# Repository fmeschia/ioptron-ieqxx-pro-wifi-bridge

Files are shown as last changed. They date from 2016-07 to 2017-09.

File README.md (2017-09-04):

# Wi-Fi to RS-232 bridge for iOptron iEQ Pro mounts

An ESP8266 and [esp-link](https://github.com/jeelabs/esp-link)-based Wi-Fi to RS-232 bridge to allow TCP wireless control of an iOptron iEQ Pro mount (tested on iEQ45 Pro, should also work on iEQ30 Pro).

[Here](https://www.youtube.com/watch?v=_uhQ0Lzc3-E) you can find a video of the operation an iEQ45 Pro mount with this circuit and the commercial Sky Safari app.

## Features
* Uses an inexpensive ESP8266 ESP-01 module
* Uses the well tested [esp-link](https://github.com/jeelabs/esp-link) open source firmware to implement a transparent TCP-to-serial bridge
* Powered directly from the mount, via the iOptron port, with an efficient 3.3V DC-to-DC converter based on the MC34063 switch-mode converter
* RS-232 compatibility ensured by a MAX3232 driver/receiver
* Easy to build, with through-hole parts and protoboard-friendly design

## Disclaimer
This project comes with no warranty. The project files may contain mistakes and errors. If you build this circuit, it is solely your responsibility to make sure that it doesn't damage your mount or other equipment, and doesn't hurt you or other people. Test all voltages and polarities before making any connections. By building the circuit you accept that I will have no liability whatsoever for damages or injuries that you or other parties may incur in during the building process or during the operation of the circuit. Builder assumes all risks. Don't build this circuit if you don't agree!

## Building instructions
### 1. Flash the ESP-01 module
The ESP-01 module must be flashed with the esp-link firmware. I have tested version 2.2.3 and it works well.
In order to flash the module, I recommend following the instructions present on the [release page](https://github.com/jeelabs/esp-link/releases/tag/v2.2.3) of the esp-link GitHub repository. Remember to enable flash programming mode by tying GPIO0 to ground and rebooting the module, before trying to upload the firmware code. The following is a schematic of how one should connect the ESP-01 module to a FTDI232 3.3V breakout board like the one sold by Sparkfun:

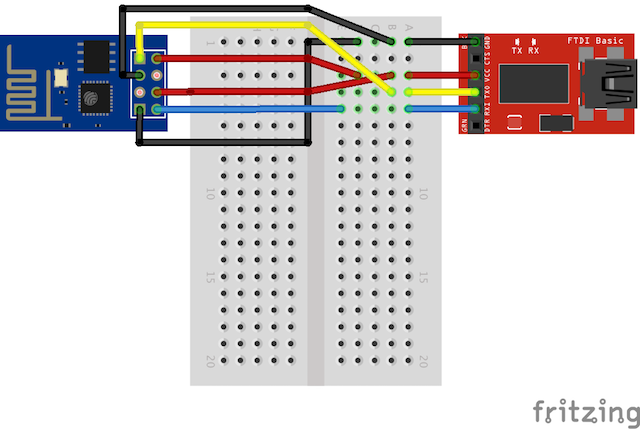
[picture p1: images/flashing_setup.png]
Flashing setup Hardware setup for flashing via USB


In my case, I used a 8-Mbit ESP-01 module, and in order to flash it (from a macOS system) I first installed esptool 1.1:

    $ curl -L https://github.com/themadinventor/esptool/archive/v1.1.tar.gz | tar xzf -
    $ cd esptool-1.1
    $ sudo python setup.py install

And then I used the following commands:

    $ curl -L https://github.com/jeelabs/esp-link/releases/download/v2.2.3/esp-link-v2.2.3.tgz | tar xzf -
    $ cd esp-link-v2.2.3
    $ esptool.py --port /dev/tty.usbserial-A601LLNU --baud 460800 write_flash -fs 8m -ff 40m 0x00000 boot_v1.5.bin 0x1000 user1.bin 0x7E000 blank.bin
    esptool.py v1.1
    Connecting...
    Running Cesanta flasher stub...
    Flash params set to 0x0020
    Writing 4096 @ 0x0... 4096 (100 %)
    Wrote 4096 bytes at 0x0 in 0.1 seconds (292.3 kbit/s)...
    Writing 307200 @ 0x1000... 307200 (100 %)
    Wrote 307200 bytes at 0x1000 in 7.1 seconds (347.0 kbit/s)...
    Writing 4096 @ 0x7e000... 4096 (100 %)
    Wrote 4096 bytes at 0x7e000 in 0.1 seconds (298.3 kbit/s)...
    Leaving...

### 2. Configure the esp-link bridge
After successfully flashing the ESP8266 module, you should power it down, remove the connection from GPI0 to ground, then power it up again and configure it. I recommend *not* powering it from USB via the FTDI232 board for this, because it doesn't really supply enough current for the ESP8266 in normal operation. Instead, power it from a regulated 3.3V (*not* 5V, it would burn it instantly!) power supply capable of delivering 0.5A.
Once powered up, a new Wi-Fi network with name "ESP_xxxx" should be visible. After connecting to that network, point your browser to http://192.168.4.1. If everything works fine, the browser should show the esp-link web interface. As a bare minimum, there are three configuration steps to do:

1. Configure the pin preset to "esp-01" 

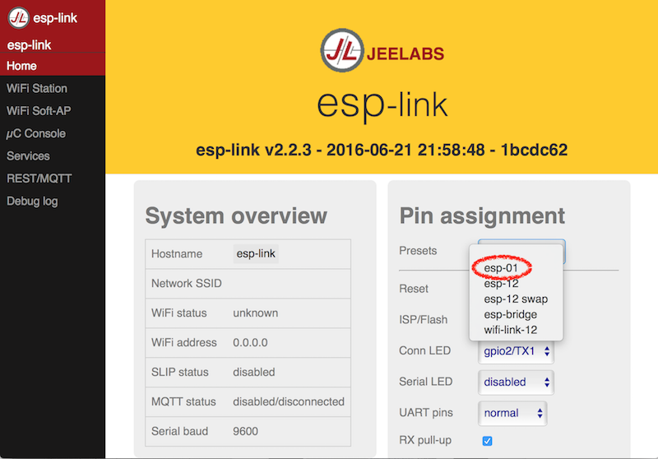
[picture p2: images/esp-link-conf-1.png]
Esp-link-pin-preset esp-link pin preset
    

2. Configure the serial port to 9600 bps, 8 data bits, 1 stop bit, no parity (9600 8N1) 

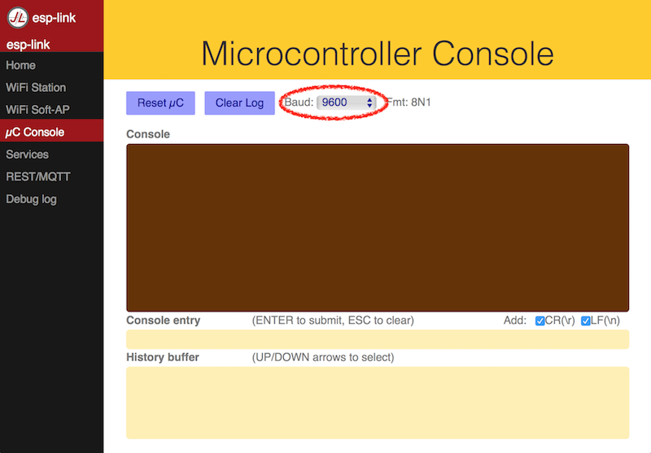
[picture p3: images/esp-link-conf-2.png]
Esp-link-bps esp-link serial port rate
    

3. Disable the UART debug log 

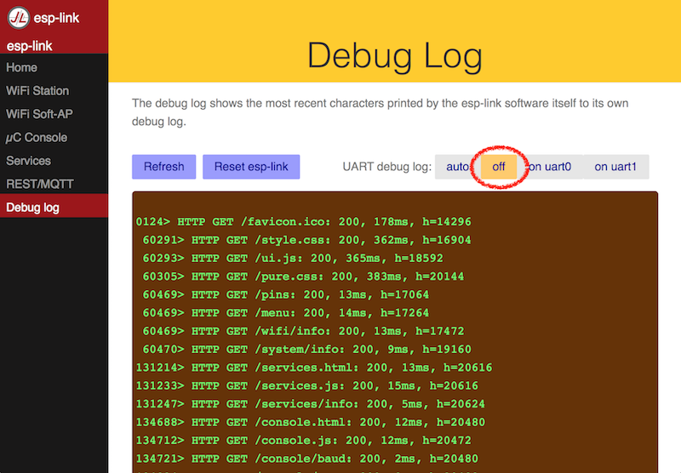
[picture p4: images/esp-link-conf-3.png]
Esp-link-debug-log esp-link debug log preset
    

You will also probably want to change the WiFi network name and its security, but that's up to personal preference.

### 3. Build the circuit
The EAGLE board file is easy to follow and transfer to a protoboard. The "traces" on the bottom layer are meant to be solder bridges between adjacent copper pads of the protoboard, whereas the air wires are meant to be real jumper wires. When the wire connects directly to a part lead, it is meant to be routed on the bottom of the board. When there are vias, the idea is that the wire can be routed on the top of the board, but of course that's just a suggestion.

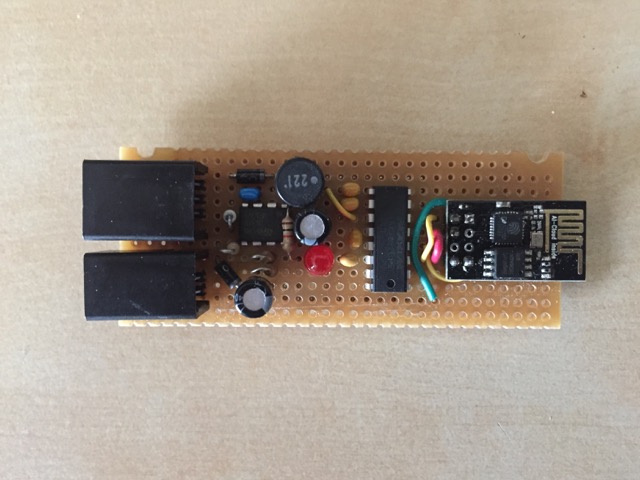
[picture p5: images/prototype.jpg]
Prototype Prototype on protoboard

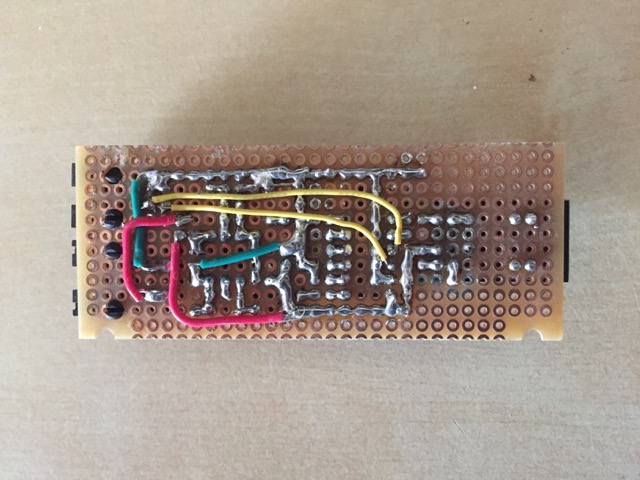
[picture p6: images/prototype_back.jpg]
Prototype back Backside of the prototype board


The project also includes an Eagle file for a simple through-hole-parts PCB. It is essentially a single-sided board: all the traces are routed on the solder side, and the component side has just a ground plane. The ground plane, on both sides, stops short of the ESP8266 trace antenna.

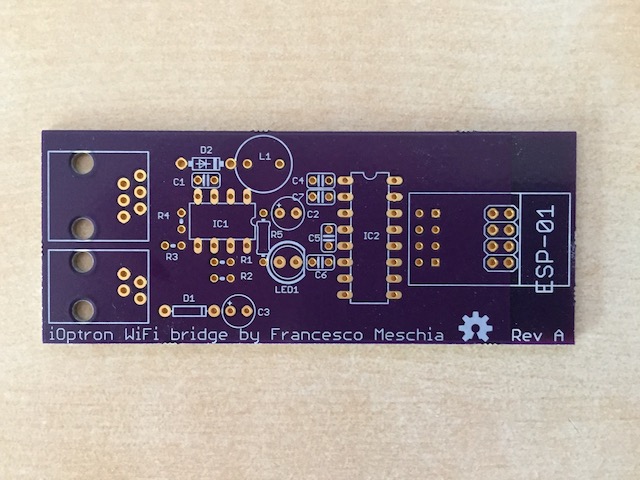
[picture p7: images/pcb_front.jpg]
PCB front Front side of the PCB

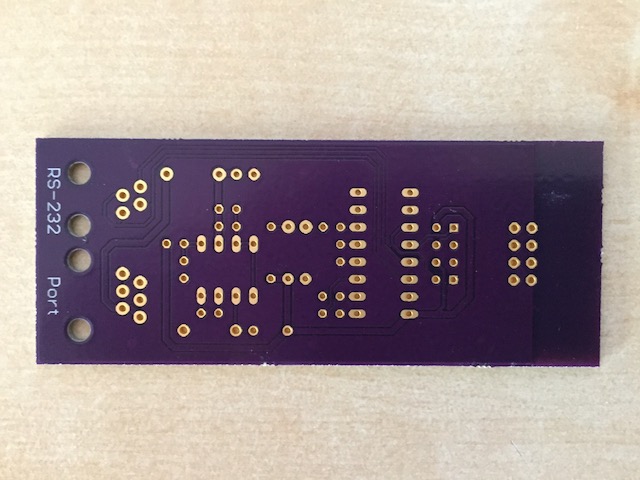
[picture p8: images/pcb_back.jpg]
PCB back Back side of the PCB

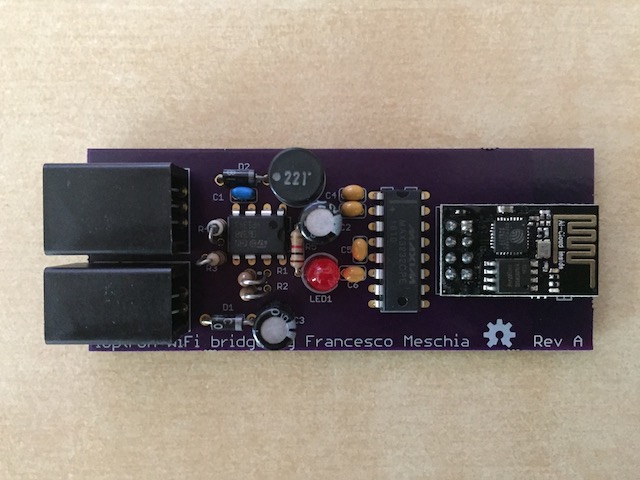
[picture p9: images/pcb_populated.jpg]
PCB populated The populated PCB


## Usage
### Connection
To connect the circuit to the mount, you need to use two cords: 
* a "straight" 6P6C cord to connect the circuit to the iOptron port on the mount (for 12V power)
* a "straight" 4P4C cord to connect the circuit to the RS-232 port on the mount

"Straight" cords are cords in which the order of the colors of the inner wires is the same if you look at both plugs (when observed from the same side). The coiled cords that came with the mount came are straight cords:

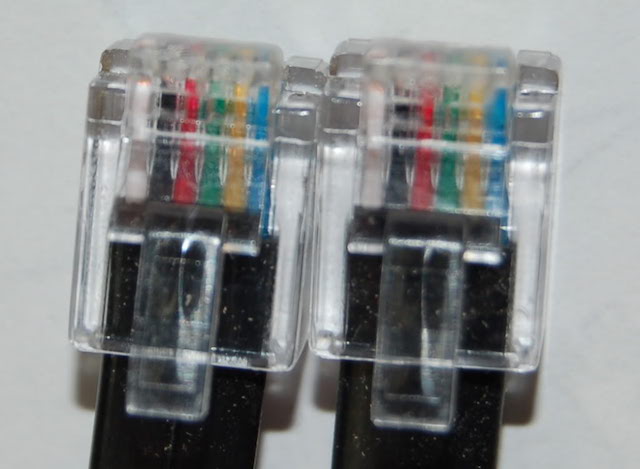
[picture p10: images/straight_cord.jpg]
Straight cord plugs Plugs of a straight cord


*A 6P6C straight cord*
### Power it up
The bridge draws power directly from the mount. When the mount is powered up, the board is also energized and the LED should light up.
### Test it
If you have a digital mixed-signal oscilloscope, you can test if the board works properly by capturing the output of the RXD pin of the RS-232 port while connected to the ESP8266 Wi-Fi AP and while sending a string to the TCP port 23 of the ESP8266 IP address (by default, 192.168.4.1). Here is a sample screenshot of the output of a USB logic analyzer while sending the string "HELLO" (ASCII 0x48 0x45 0x4C 0x4C 0x4F plus a 0x0A newline) to the bridge board:

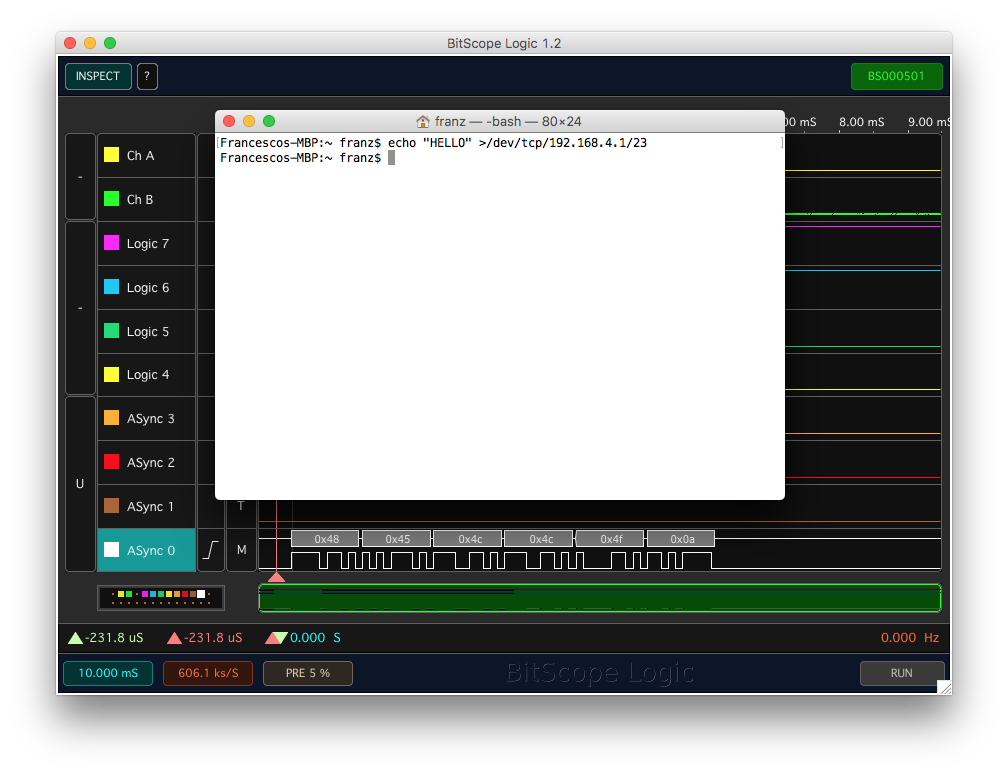
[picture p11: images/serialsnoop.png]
Logic analyzer output

### Enjoy!
Point your favorite telescope control software to 192.168.4.1, port 23, and enjoy wireless telescope control!

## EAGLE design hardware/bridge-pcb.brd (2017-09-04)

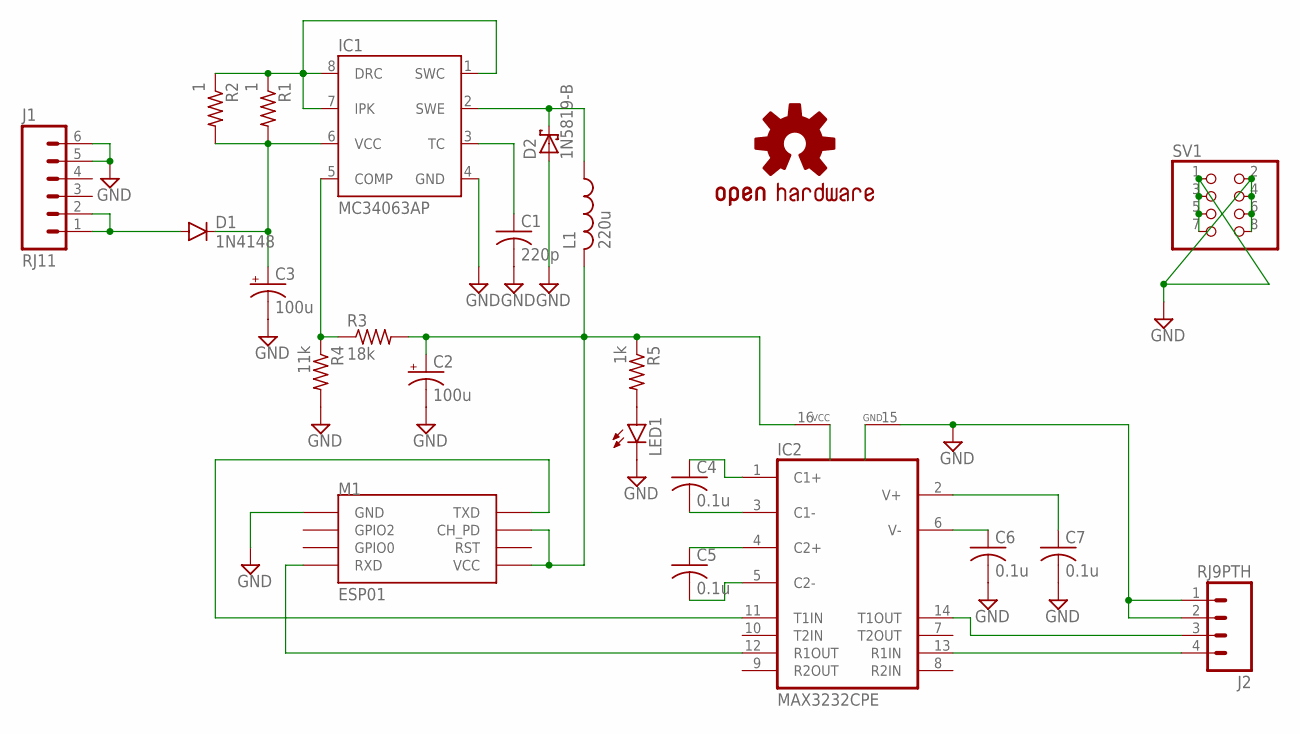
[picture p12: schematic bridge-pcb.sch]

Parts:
C1: 220p; C025-024X044
C2, C3: 100u; E2,5-5
C4, C5, C6, C7: 0.1u; C025-024X044
D1: 1N4148; DIODE-1N4148
D2: 1N5819-B; DO41-7.6
IC1: MC34063AP; DIL-08
IC2: MAX3232CPE; DIL16
J1: RJ11; RJ11-6
J2: RJ9PTH; RJ9
L1: 220u; 6000-XXXX-RC
LED1: LED5MM
LOGO1: OSHW-LOGOM; OSHW-LOGO-M
M1: ESP01
R1, R2: 1; 0204V
R3: 18k; 0204V
R4: 11k; 0204V
R5: 1k; 0204/7
SV1: PINHD-2X4; 2X04

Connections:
3V3: C2.+, IC2.16 (VCC), L1.2, M1.CH_PD, M1.VCC, R3.2, R5.1
12V: C3.+, D1.C, IC1.6 (VCC), R1.2, R2.2
GND: C1.2, C2.-, C3.-, C6.2, C7.2, D2.A, IC1.4 (GND), IC2.15 (GND), J1.5, J1.6, J2.1, J2.2, LED1.K (C), M1.GND, R4.2, SV1.1, SV1.2, SV1.3, SV1.4, SV1.5, SV1.6, SV1.7, SV1.8
unnamed: C1.1, IC1.3 (TC)
unnamed: LED1.A, R5.2
unnamed: D2.C, IC1.2 (SWE), L1.1
unnamed: IC2.11 (T1IN), M1.TX (TXD)
unnamed: IC2.12 (R1OUT), M1.RX (RXD)
unnamed: C4.2, IC2.3 (C1-)
unnamed: C4.1, IC2.1 (C1+)
unnamed: C5.1, IC2.4 (C2+)
unnamed: C5.2, IC2.5 (C2-)
unnamed: C6.1, IC2.6 (V-)
unnamed: C7.1, IC2.2 (V+)
unnamed: IC2.14 (T1OUT), J2.3
unnamed: IC2.13 (R1IN), J2.4
unnamed: IC1.1 (SWC), IC1.7 (IPK), IC1.8 (DRC), R1.1, R2.1
unnamed: IC1.5 (COMP), R3.1, R4.1
VBATT: D1.A, J1.1, J1.2

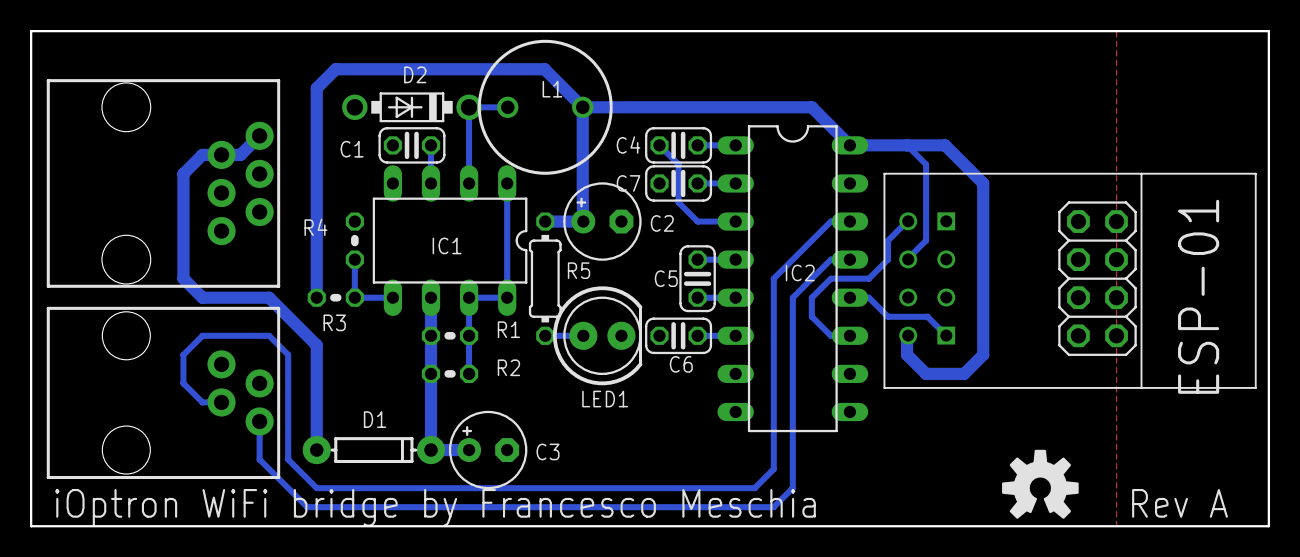
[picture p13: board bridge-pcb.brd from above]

Board: 2 copper layers, 82.5 x 33.0 mm, 23 parts (0 on the bottom side), 19 nets.

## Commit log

2016-07-30 Minor design and documentation changes
    [bridge.brd, bridge.sch]
2016-07-30 Minor board beauty treatment
    [bridge.brd, bridge.sch]
2016-11-14 Small board changes
    [bridge.brd, bridge.sch]
2016-12-30 Doc changes. Added one-layer PCB ready for fabrication (e.g. via OSH Park).
    [bridge-pcb.brd, bridge-pcb.sch]
2017-01-14 Tweaked fonts and layers in PCB
    [bridge-pcb.brd]
2017-06-22 Added BOM
2017-09-04 Added pin header footprint to provide support for the ESP8266 module
    [bridge-pcb.brd, bridge-pcb.sch]

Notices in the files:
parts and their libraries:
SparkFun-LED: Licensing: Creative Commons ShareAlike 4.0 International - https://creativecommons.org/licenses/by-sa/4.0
